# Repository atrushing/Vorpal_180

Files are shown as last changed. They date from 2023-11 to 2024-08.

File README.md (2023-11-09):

# Vorpal 180 -- PRE-RELEASE --

    A printed printer

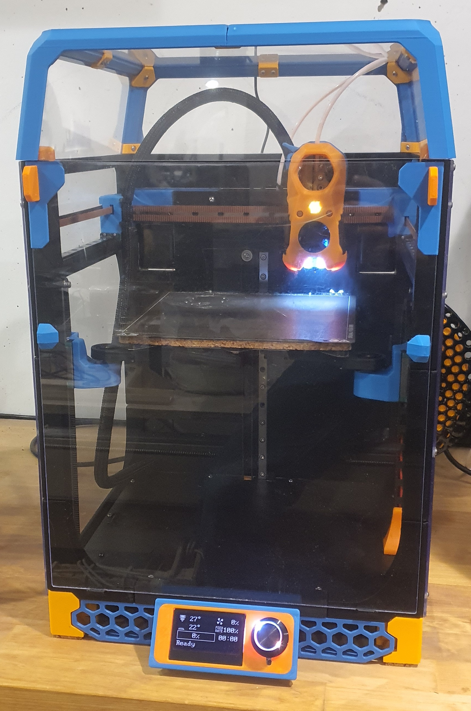
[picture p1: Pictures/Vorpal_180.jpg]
Vorpal 180


## Features:

- Print volume: 180 x 180 x 200mm

- Triple belted Z

- 3:1 geared Z with Nema 17 steppers or 5:1 with Nema 14 pancake steppers

- MGN12  X axis

- MGN9 option for Boop compatibility

- MGN9  Y and Z axes

- Design based on Voron V0.1 and Trident printers

- Bed and sub-plate from Prusa Mini

- Uses printed flexures instead of GE5C bearings for build plate mounting

- Hidden handles in side skirts

- Hinged locking tophat

- Mini Stealth toolhead compatible - [1.5](https://www.teamfdm.com/files/file/606-mini-stealth-orbiter-15/) [2.0](https://www.teamfdm.com/files/file/612-mini-stealth-orbiter-20/) [LGX](https://www.teamfdm.com/files/file/616-mini-stealth-lgx-lite/) [Sherpa](https://www.teamfdm.com/files/file/657-mini-stealth-mini-sherpa/)

- Manta M8P control board

Learn more and follow the development process on [TeamFDM.com](https://www.teamfdm.com/forums/topic/1886-vorpal-180-a-printed-printer/)

[Support me](https://paypal.me/atrushing)

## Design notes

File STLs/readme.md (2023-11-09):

## Filament Required

### Base color
- 900 grams

### Primary color
- 500 grams

### Accent color
- 200 grams

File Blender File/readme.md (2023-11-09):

This project was developed entirely in Blender. The official geometry is found in the STLs folder and only exists in mesh format.

The .blend file provided here is intended as a reference for assembly and modding purposes.

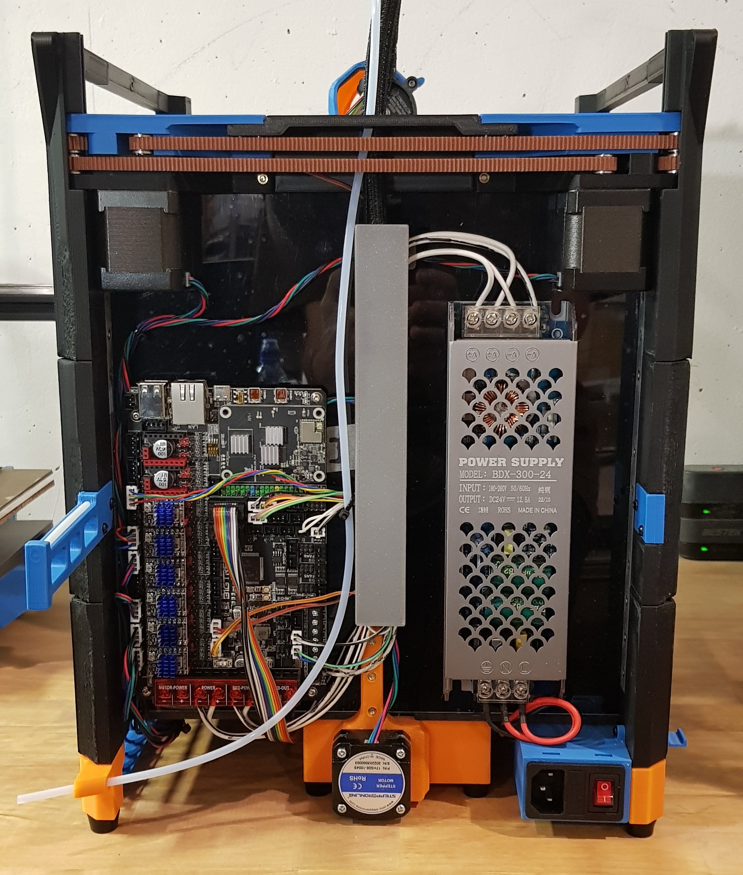
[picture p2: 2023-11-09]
Pictures/Electronics_bay.jpg

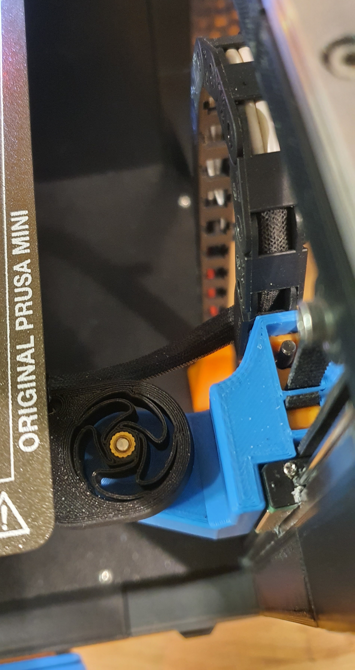
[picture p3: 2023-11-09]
Pictures/Z Bed Joint Flexure.jpg

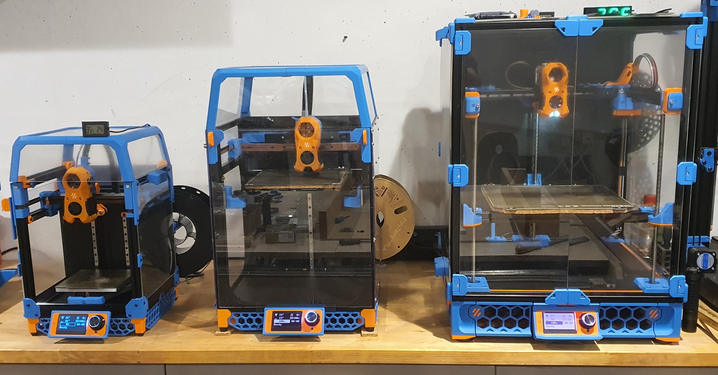
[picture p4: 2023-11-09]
Pictures/Comparison.jpg

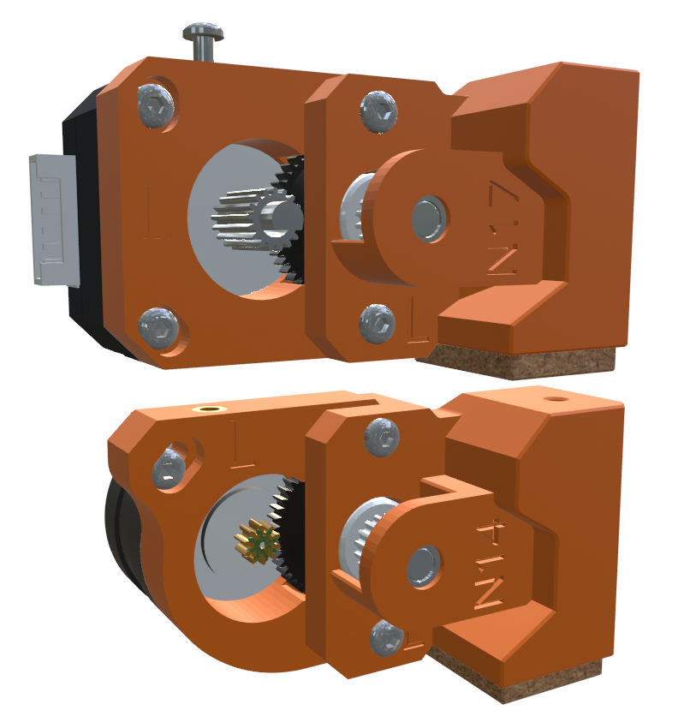
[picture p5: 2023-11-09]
Pictures/Belt driven Z axis options.png

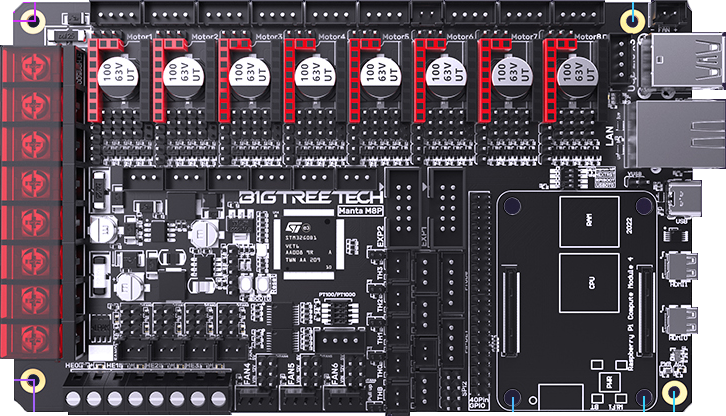
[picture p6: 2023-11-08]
Blender File/BTT_Manta_M8P_cr.png

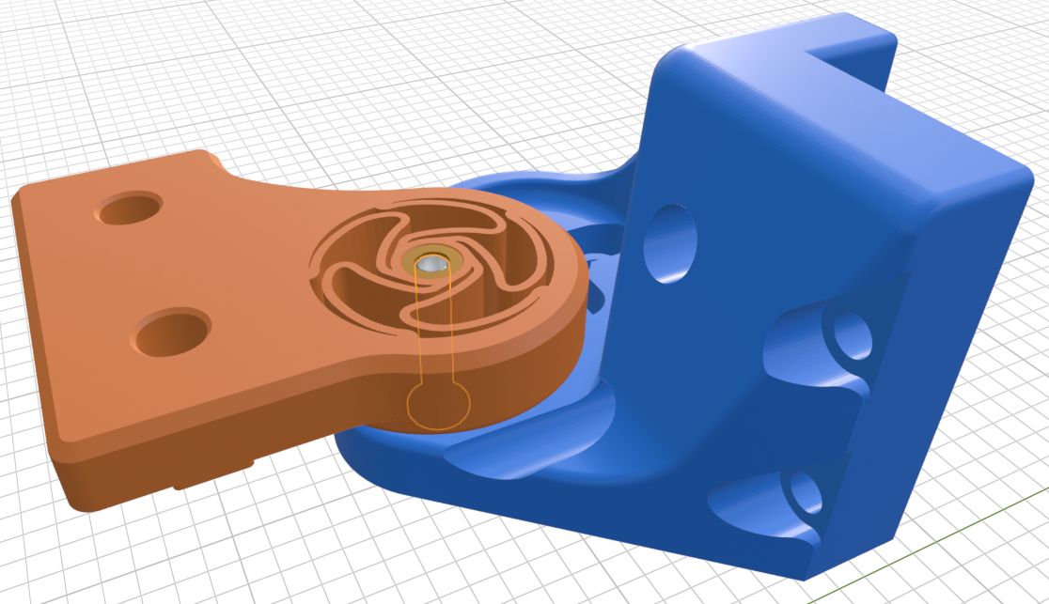
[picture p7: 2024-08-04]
STLs/Z_Axis/Trident_Flexures/Trident_Flexures.png

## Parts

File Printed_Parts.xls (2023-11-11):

Group | Name | Qty | Color | Finished | Source | License
Base | [a]_12864_display_case_front_insert.stl | 1 | Accent
 | [a]_Display_wedge_mount_35deg.stl | 1 | Accent
 | [a]_Foot_rear_left.stl | 1 | Accent
 | [a]_Foot_rear_right.stl | 1 | Accent
 | [p]_12864_display_case_front.stl | 1 | Primary
 | [p]_12864_display_case_rear.stl | 1 | Primary
 | [p]_Door_stow_blank_x2.stl | 2 | Primary
 | [p]_Door_stow_hook_x2.stl | 2 | Primary
 | [p]_Side_skirt_front.stl | 1 | Primary
 | [p]_Side_skirt_left.stl | 1 | Primary
 | [p]_Side_skirt_right.stl | 1 | Primary
Nema 14 | [a]_Foot_front_left_Nema14.stl | option | Accent
 | [a]_Foot_front_right_Nema14.stl | option | Accent
 | [a]_Motor_mount_front_left_Nema14.stl | option | Accent
 | [a]_Motor_mount_front_right_Nema14.stl | option | Accent
 | [a]_Motor_mount_rear_Nema14.stl | option | Accent
 | [a]_Z_axis_drive_rear_Nema14.stl | option | Accent
Nema 17 | [a]_Foot_front_left_Nema17.stl | 1 | Accent
 | [a]_Foot_front_right_Nema17.stl | 1 | Accent
 | [a]_Motor_mount_front_left_Nema17.stl | 1 | Accent
 | [a]_Motor_mount_front_right_Nema17.stl | 1 | Accent
 | [a]_Motor_mount_rear_Nema17.stl | 1 | Accent
 | [a]_Z_axis_drive_rear_Nema17.stl | 1 | Accent
 |  | 19
Electronics Bay | [p]_Manta_M8P_mounts.stl | 1 set | Primary
 | [p]_Power_inlet.stl | 1 | Primary
 | [p]_Spool_holder.stl | 1 | Primary
 | [p]_Spool_holder_blank.stl | 1 | Primary
 | [p]_Wire_guide.stl | 1 | Primary |  | remixed from https://www.printables.com/model/118343-cable-rail-cable-guide | Public Domain | https://creativecommons.org/share-your-work/public-domain/cc0/
 | [p]_Wire_guide_cover.stl | 1 | Primary |  | remixed from https://www.printables.com/model/118343-cable-rail-cable-guide | Public Domain | https://creativecommons.org/share-your-work/public-domain/cc0/
 | [p]_Z_axis_rear_stiffener_x2.stl | 2 | Primary
 |  | 8
Frame | [b]_AB_drive_frame_center.stl | 1 | Base
 | [b]_A_drive_frame_lower.stl | 1 | Base
 | [b]_A_drive_frame_upper.stl | 1 | Base
 | [b]_B_drive_frame_lower.stl | 1 | Base
 | [b]_B_drive_frame_upper.stl | 1 | Base
 | [b]_Frame_center_connector_left.stl | 1 | Base
 | [b]_Frame_center_connector_right.stl | 1 | Base
 | [b]_Frame_front_lower_connector.stl | 1 | Base
 | [b]_Frame_front_lower_left.stl | 1 | Base
 | [b]_Frame_front_lower_right.stl | 1 | Base
 | [b]_Frame_front_upper_left.stl | 1 | Base
 | [b]_Frame_front_upper_right.stl | 1 | Base
 | [b]_Frame_front_vertical_connector_left.stl | 1 | Base
 | [b]_Frame_front_vertical_connector_right.stl | 1 | Base
 | [b]_Frame_lower_connecter_left.stl | 1 | Base
 | [b]_Frame_lower_connecter_right.stl | 1 | Base
 | [b]_Frame_rear_lower_left.stl | 1 | Base
 | [b]_Frame_rear_lower_right.stl | 1 | Base
 | [b]_Frame_rear_upper_left.stl | 1 | Base
 | [b]_Frame_rear_upper_right.stl | 1 | Base
 | [b]_Frame_rear_vertical_connector_left.stl | 1 | Base
 | [b]_Frame_rear_vertical_connector_right.stl | 1 | Base
 | [b]_Frame_upper_connector_left.stl | 1 | Base
 | [b]_Frame_upper_connector_right.stl | 1 | Base
 |  | 24
Gantry | [a]_AB_tension_idler_new_x2.stl | 2 | Accent
 | [a]_AB_tension_idler_old_x2.stl | 2 | Accent
 | [p]_X_Axis_brace_MGN9_left.stl | option | Primary
 | [p]_X_Axis_brace_MGN9_right.stl | option | Primary
 | [p]_X_Axis_brace_MGN12_left.stl | 1 | Primary
 | [p]_X_Axis_brace_MGN12_right.stl | 1 | Primary
 | [p]_x_frame_Mini_Stealth_MicroProbe_left.stl | 1 | Primary
 | [p]_x_frame_Mini_Stealth_MicroProbe_right.stl | 1 | Primary
 | [p]_XY_joint_left_lower.stl | 1 | Primary
 | [p]_XY_joint_left_upper.stl | 1 | Primary
 | [p]_XY_joint_right_lower.stl | 1 | Primary
 | [p]_XY_joint_right_upper.stl | 1 | Primary
 |  | 12
Panels | [a]_door_panel_pinch_handle_x2.stl | 2 | Accent
 | [p]_door_panel_magnet_latch_x4.stl | 4 | Primary
 | [p]_3mm_door_panel_corner_top_left.stl | 1 | Primary
 | [p]_3mm_door_panel_corner_top_right.stl | 1 | Primary
 |  | 8
 | 3mm_back_aux_panel_black.stl | 1 | black
 | 3mm_back_main_panel_black.stl | 1 | black
 | 3mm_door_panel_clear.stl | 1 | clear
 | 3mm_side_left_panel_clear.stl | 1 | clear
 | 3mm_side_right_panel_clear.stl | 1 | clear
 | 3mm_tophat_front-back_panel_clear_x2.stl | 2 | clear
 | 3mm_tophat_side_panel_clear_x2.stl | 2 | clear
 | 3mm_tophat_top_panel_clear.stl | 1 | clear
 | 4mm_bottom_panel_black.stl | 1 | black
 |  | 11
Tools | AB_pulley_jig.stl | 1
 | Calibration_square_100mm.stl | 1
 | Calibration_square_100mm_base.stl | 1
 | Kezat_Hex_Bit_Driver_Short_Thumb_Crown.stl | 3 |  |  | remixed from https://www.printables.com/model/16567-screwdriver | CC4 Attribution | http://creativecommons.org/licenses/by/4.0/
 | Hex Bit Set |  |  |  | https://www.amazon.de/-/en/Racing-4-Piece-Metric-Electric-Screw/dp/B097NF94SL/
 | MicroSD_card_tweezers.stl | 1
 | Snap_pin_x26.stl | 26 | Primary |  | https://www.thingiverse.com/thing:213310 | CC3 Attribution | https://creativecommons.org/licenses/by-sa/3.0/
 |  | 33
Top Hat | [a]_Tophat_clips_plate.stl | 1 set | Accent
 | [p]_tophat_latch_thumbscrew_x2.stl | 2 | Primary
 | [p]_Tophat_part_front_left.stl | 1 | Primary
 | [p]_Tophat_part_front_right.stl | 1 | Primary
 | [p]_Tophat_part_rear_left.stl | 1 | Primary |  | remixed from https://www.teamfdm.com/files/file/327-tophathingev01/ | GPL v3
 | [p]_Tophat_part_rear_right.stl | 1 | Primary |  | remixed from https://www.teamfdm.com/files/file/327-tophathingev01/ | GPL v3
 | [p]_Unibody_Tophat.stl | option | Primary
 |  | 7
Z Axis | [a]_belt_lock_wedge_x3.stl | 3 | Accent
 | [a]_belt_tension_slider_left.stl | 1 | Accent
 | [a]_belt_tension_slider_rear.stl | 1 | Accent
 | [a]_belt_tension_slider_right.stl | 1 | Accent
 | [a]_Cable_chain_mount_base.stl | 1 | Accent
 | [b]_Cable_chain_guide.stl | 1 | Base
 | [b]_Z_bed_left.stl | 1 | Base
 | [b]_Z_bed_rear.stl | 1 | Base
 | [b]_Z_bed_right.stl | 1 | Base
 | [p]_Z_carriage_left.stl | 1 | Primary
 | [p]_Z_carriage_rear.stl | 1 | Primary
 | [p]_Z_carriage_right.stl | 1 | Primary
 |  | 14

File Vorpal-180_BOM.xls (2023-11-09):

Movement |  |  |  |  |  |  | €
MGN9H | 5 | 250mm | €12.48 | €62.40 | Amazon.com
MGN12H | 1 | 250mm | €17.01 | €17.01 | Amazon.com
GT2 belt | 1 | 4m20 | €15.59 | €14.99 | Amazon.com
GT2 16T Pulley | 3 | 5mm bore | €1.40 | €4.20 | Amazon.com
Nema17 x 20 | 3 | Z Axis | €7.46 | €22.38 | https://www.omc-stepperonline.com/nema-17-bipolar-1-8deg-16ncm-22-6oz-in-1a-3-7v-42x42x20mm-4-wires-17hs08-1004s
Option |  | LDO | €22.46 |  | https://www.aliexpress.com/item/1005002899860754.html
Nema17 x 40 | 2 | A/B Motors | €9.94 | €19.88 | https://www.omc-stepperonline.com/nema-17-bipolar-45ncm-64oz-in-2a-42x42x40mm-4-wires-w-1m-cable-connector-17hs16-2004s1
BMG Kit | 3 | Z axis reduction | €5.07 | €15.21 | https://www.aliexpress.com/item/1005004946578945.html
F623 Flanged Bearing | 30 | Belt management | €1.44 | €43.20 | Amazon.com
M3x6x0.5 Shim | 45 | 3 shims per 2 bearings | €0.12 | €5.31 | Amazon.com
3mm x 20mm steel shaft | 4 | pin mod for XY-joints
Toolhead
4010 Blower | 2 | 24V | €4.48 | €8.96 | Amazon.com
3007/3010 fan | 1 | 5V/24V | €3.90 | €3.90 | Amazon.com
BMG Kit | 1 | Mini/Micro Sherpa | €5.07 | €5.07 | https://www.aliexpress.com/item/1005004946578945.html
Nema14 Pancake 20mm long | 1 | StepperOnline | €9.15 | €9.15 | https://www.omc-stepperonline.com/nema-14-high-temp-stepper-motor-10ncm-14-24oz-in-insulation-class-h-180c-14re08-1004s-h
4mm OD x 2mm ID PTFE tube |  | ~50mm
Phaetus Dragonfly | 1 |  | €61.32 | €61.32 | 3Djake.com
24V 50W heater + Thermistor | 1 |  | €4.99 | €4.99 | Amazon.com
Extra
7x7mm Cable Chain | 1 | 40cm | €9.73 | €9.73 | Amazon.com
M3 HeatSet Inserts | 100 | M3x4x5 | €0.08 | €8.30 | Amazon.com | 120 pcs for $10.03
Rubber Feet 15x12x8mm | 6 |  | 0.58 | 3.48 | Amazon.com
6mm cork 20x25mm feet | 4 |  | €0.15 | €0.60 | local
4mm OD x 3mm ID PTFE tube | 1 | reverse bowden | €5.94 | €5.94 | Amazon.com
3x6mm magnets | 8 | door latching
Buildplate
Prusa Mini bed + PEI Buildplate | 1 |  | €44.66 | €44.66 | https://www.aliexpress.com/item/4000898386404.html
Official Prusa spring steel sheet | 1 | worth getting the original | €30.00 |  | https://www.prusa3d.com/product/mini-double-sided-textured-pei-powder-coated-spring-steel-sheet/
Prusa Mini subplate | 1 |  | €15.97 | €15.97 | https://www.aliexpress.com/item/4000761390845.html
6mm x 3mm standoff 6mm long | 9 |  | €0.20 | €1.77 | https://www.aliexpress.com/item/33002300459.html
M3x16 FHCS | 9 |  | €0.15 | €1.35 | Amazon.com
GE5C Joint bearing | 3 |  | €2.14 | €6.42 | https://www.aliexpress.com/item/1005001865254355.html
6mm thick cork | 1 |  | €1.56 | €1.56 | local
Electronics
24V 300W Power Supply | 1 |  | €21.47 | €21.47 | https://www.aliexpress.com/item/32826453801.html
BTT Manta M8P w/ CB1 +TMC2209 | 1 |  | €98.68 | €98.68 | https://biqu.equipment/collections/control-board/products/manta-m4p-m8p?variant=39847239155810
BTT Mini 12864 | 1 |  | €12.68 | €12.68
Biqu MicroProbe | 1 |  | €27.28 | €27.28 | https://biqu.equipment/products/microprobe-v1-0-for-b1-printers-h2-extruders-ender-3
Power Inlet | 1 |  | €11.29 | €11.29 | Amazon.com
 |  |  |  | €559.25

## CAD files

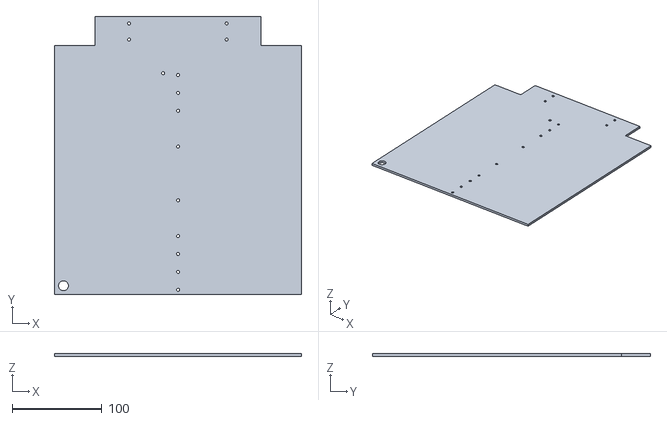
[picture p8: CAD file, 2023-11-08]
STLs/Panels/3mm_back_main_panel_black.stl
276.0 x 311.1 x 3.00

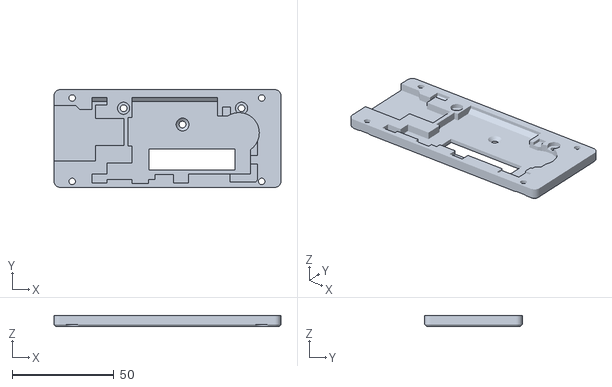
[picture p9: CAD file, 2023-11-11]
STLs/Base/[p]_12864_display_case_rear.stl
111.6 x 48.1 x 5.51

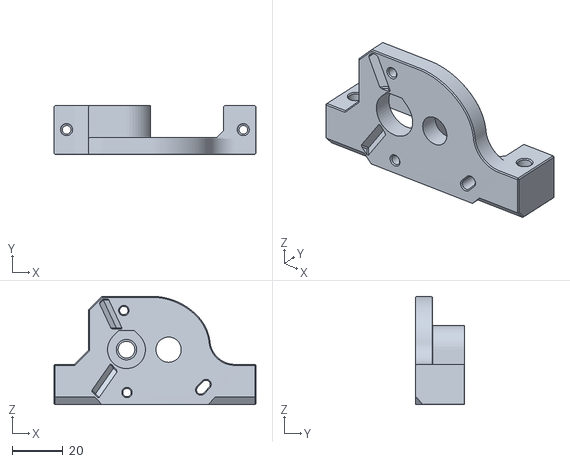
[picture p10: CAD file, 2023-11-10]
STLs/Base/Nema_14_option/[a]_Z_axis_drive_rear_Nema14.stl
80.0 x 19.4 x 42.9

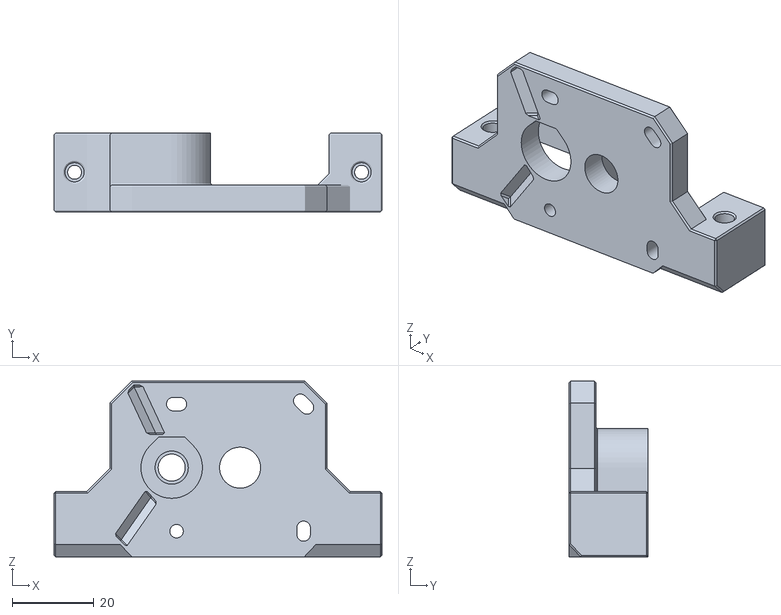
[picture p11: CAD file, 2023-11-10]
STLs/Base/Nema_17_option/[a]_Z_axis_drive_rear_Nema17.stl
80.0 x 19.3 x 42.9

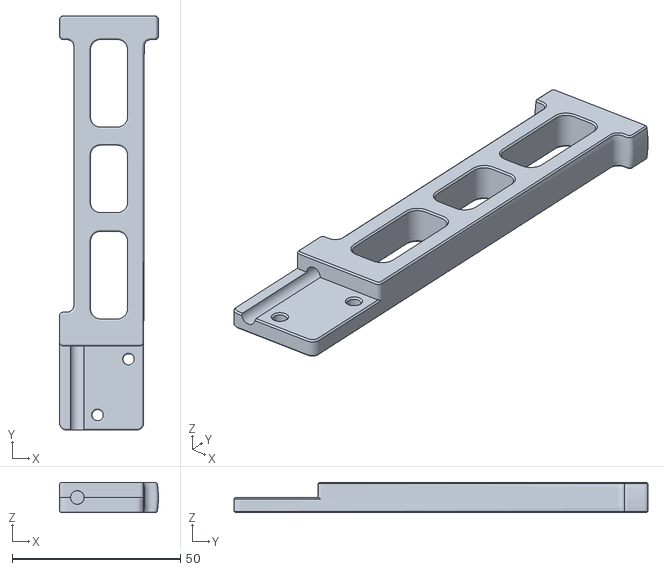
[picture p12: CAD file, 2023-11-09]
STLs/Electronics_bay/[p]_Spool_holder.stl
29.4 x 123.0 x 9.00

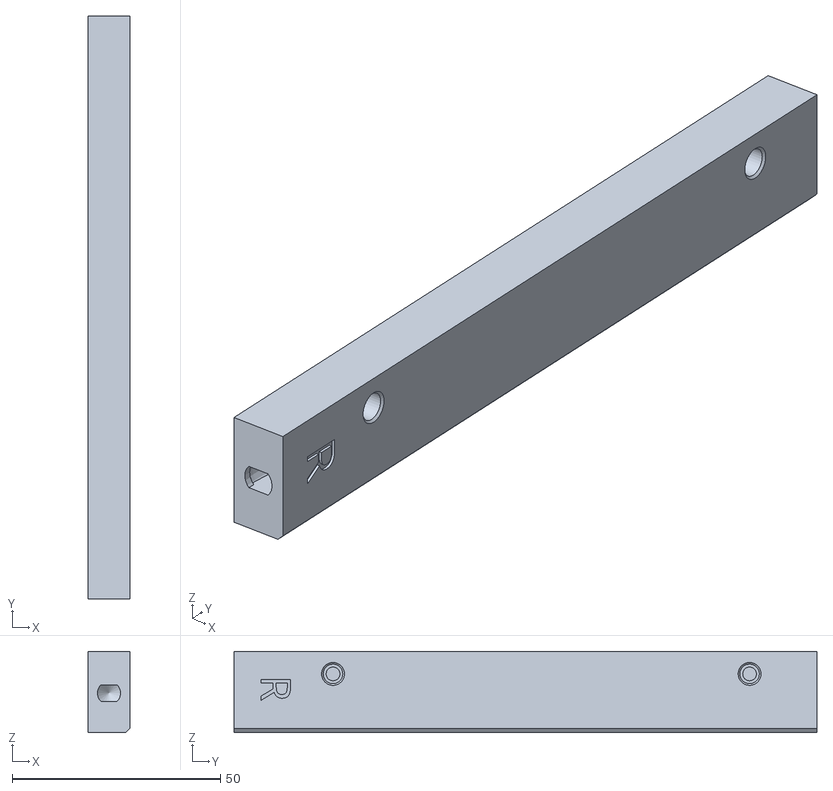
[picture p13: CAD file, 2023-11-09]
STLs/Frame/[b]_Frame_center_connector_right.stl
10.0 x 140.0 x 19.5

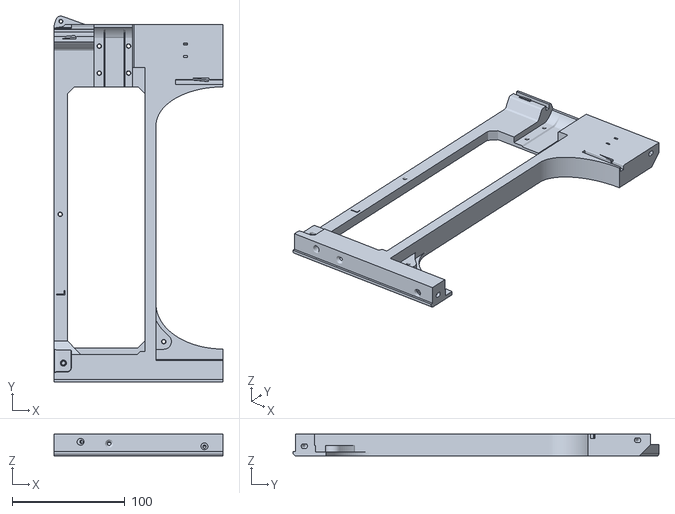
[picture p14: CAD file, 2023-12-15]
STLs/Frame/Big Printers/[b]_Frame_Left_upper.stl
150.0 x 324.9 x 19.5

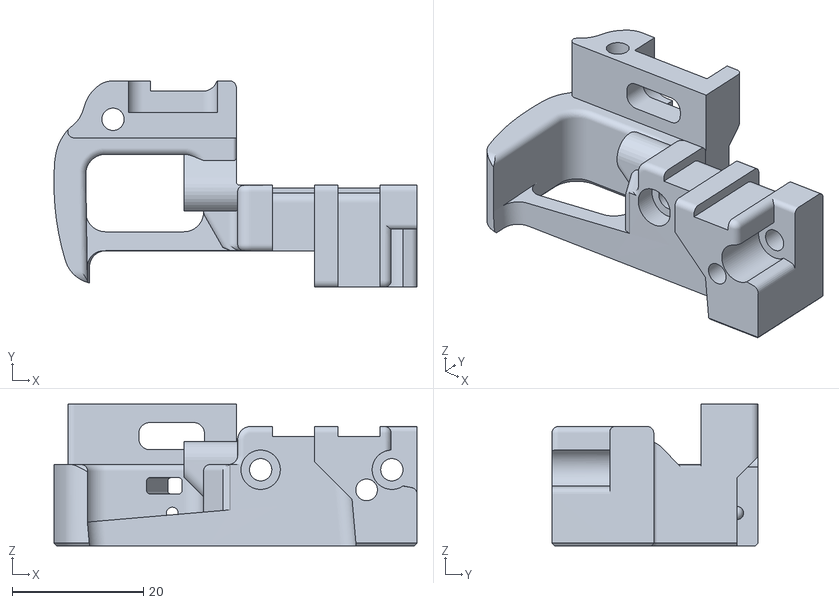
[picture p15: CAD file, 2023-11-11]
STLs/Gantry/[p]_x_frame_Mini_Stealth_MicroProbe_right.stl
55.3 x 31.4 x 21.6

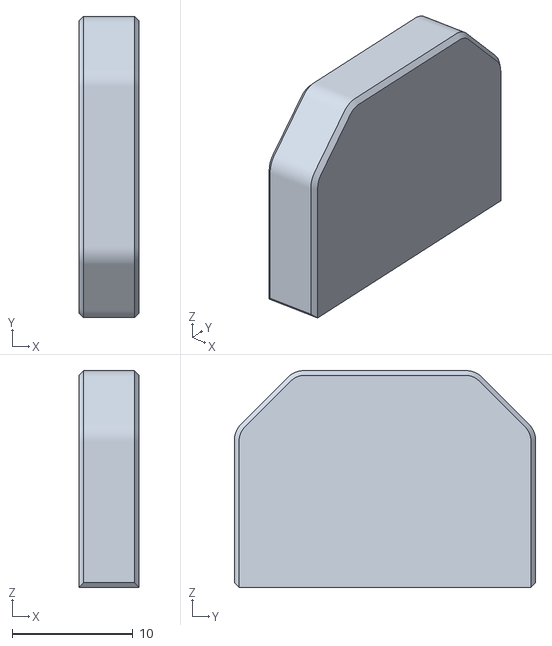
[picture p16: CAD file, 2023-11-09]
STLs/Panels/[a]_door_panel_pinch_handle_x2.stl
5.00 x 25.0 x 18.0

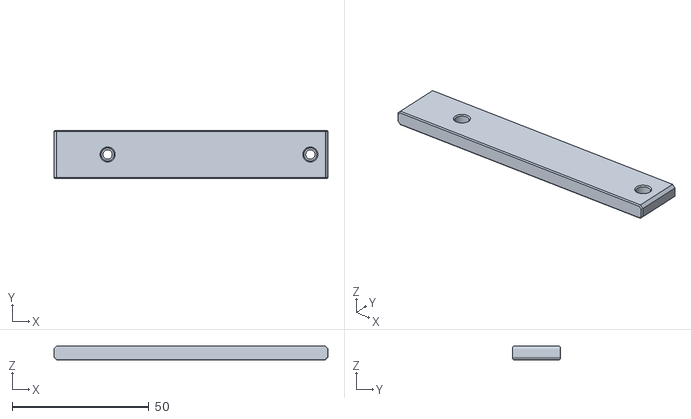
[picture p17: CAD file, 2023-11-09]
STLs/Tools/Calibration_square_100mm_base.stl
100.0 x 17.6 x 5.00

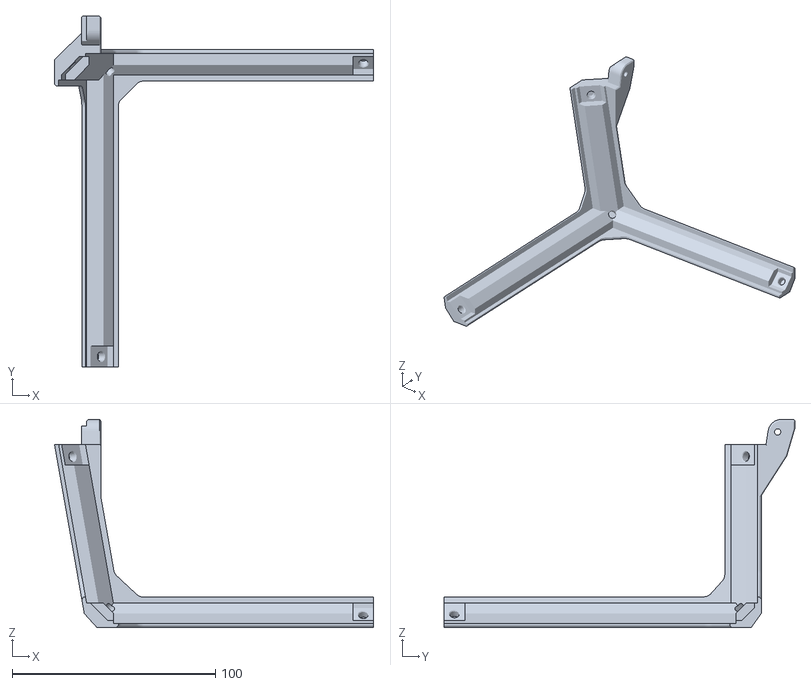
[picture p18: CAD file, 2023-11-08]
STLs/TopHat/[p]_Tophat_part_rear_right.stl
156.9 x 172.4 x 102.4

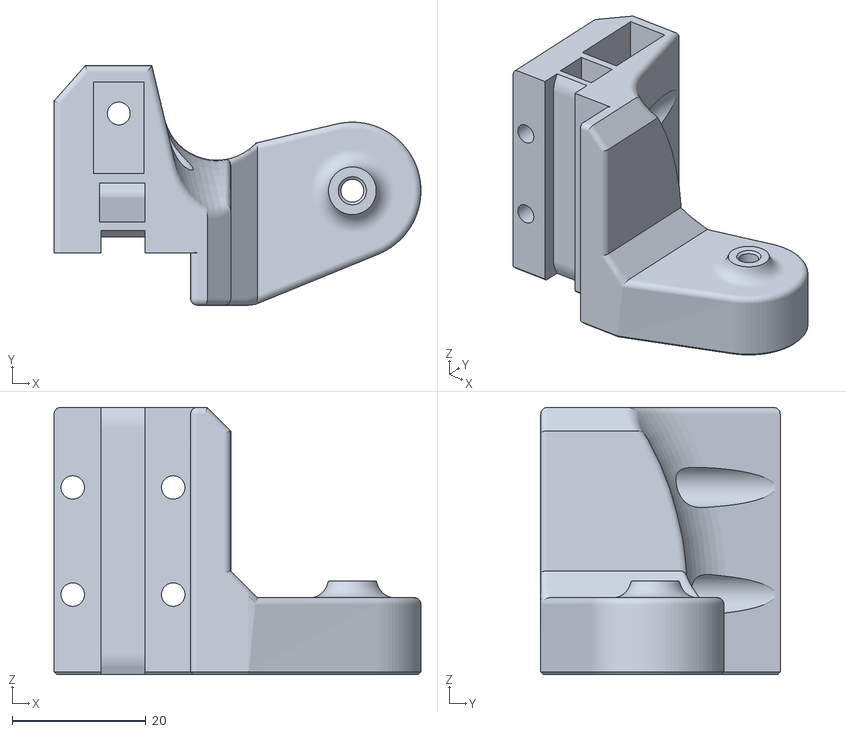
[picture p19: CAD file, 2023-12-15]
STLs/Z_Axis/[p]_Z_carriage_left_UHF.stl
54.8 x 35.8 x 39.9

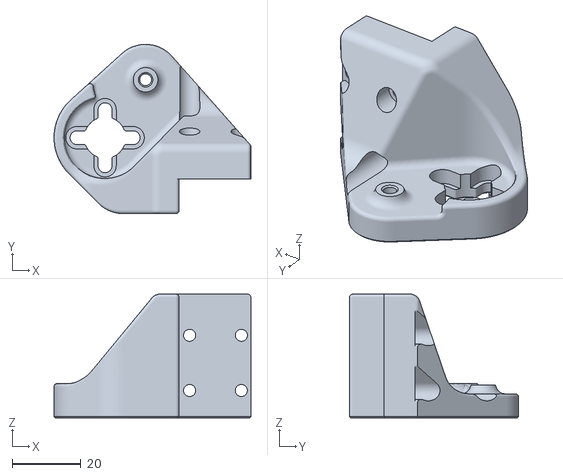
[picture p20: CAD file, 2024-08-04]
STLs/Z_Axis/Trident_Flexures/z_carriage_right_M3_Flexure.stl
57.1 x 49.1 x 35.9

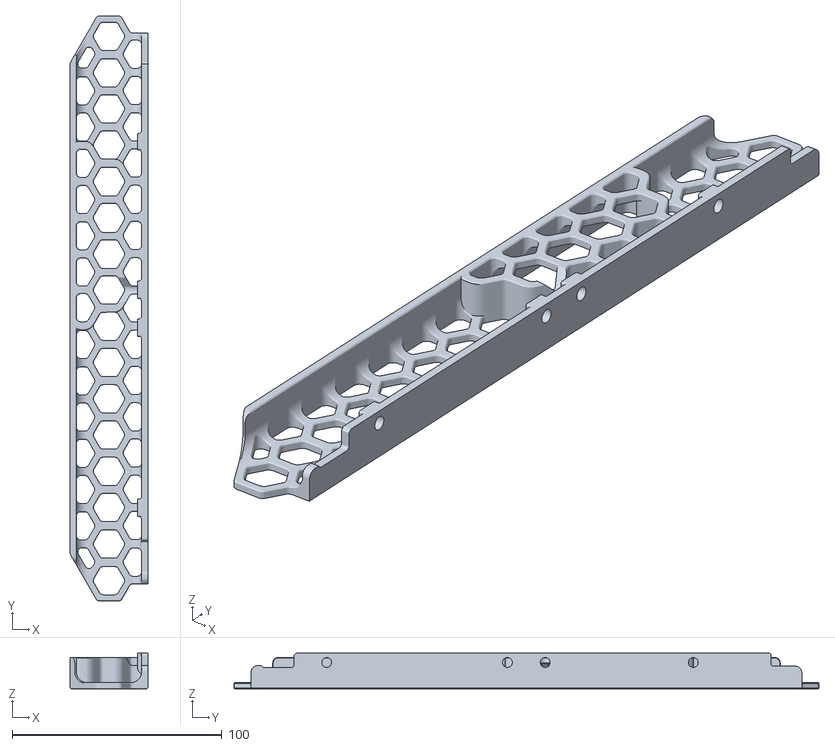
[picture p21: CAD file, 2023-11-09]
STLs/Base/[p]_Side_skirt_right.stl
37.0 x 278.7 x 17.0

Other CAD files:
STLs/Base/Nema_14_option/[a]_Motor_mount_rear_Nema14.stl
STLs/Base/Nema_17_option/[a]_Motor_mount_rear_Nema17.stl
STLs/Electronics_bay/[p]_Wire_guide_cover.stl
STLs/Frame/[b]_Frame_rear_vertical_connector_right.stl
STLs/Base/Nema_14_option/[a]_Foot_front_left_Nema14.stl
STLs/Base/Nema_14_option/[a]_Foot_front_right_Nema14.stl
STLs/Base/Nema_14_option/[a]_Motor_mount_front_left_Nema14.stl
STLs/Base/Nema_14_option/[a]_Motor_mount_front_right_Nema14.stl
STLs/Base/Nema_17_option/[a]_Foot_front_left_Nema17.stl
STLs/Base/Nema_17_option/[a]_Foot_front_right_Nema17.stl
STLs/Base/Nema_17_option/[a]_Motor_mount_front_left_Nema17.stl
STLs/Base/Nema_17_option/[a]_Motor_mount_front_right_Nema17.stl
STLs/Base/[a]_12864_display_case_front_insert.stl
STLs/Base/[a]_Display_wedge_mount_35deg.stl
STLs/Base/[a]_Foot_rear_left.stl
STLs/Base/[a]_Foot_rear_right.stl
STLs/Base/[p]_12864_display_case_front.stl
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

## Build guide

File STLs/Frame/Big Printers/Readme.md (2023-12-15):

A 400mm printer is needed to print the side frames in one solid piece. There are also two-piece side frames that can fit on a 350mm printer.
There has been no shrinkage compensation applied to these pieces as different printers and filaments will have different shrink factors. Check the Tools folder for the calibration_square and follow the process in the manual to calculate a good print scale.

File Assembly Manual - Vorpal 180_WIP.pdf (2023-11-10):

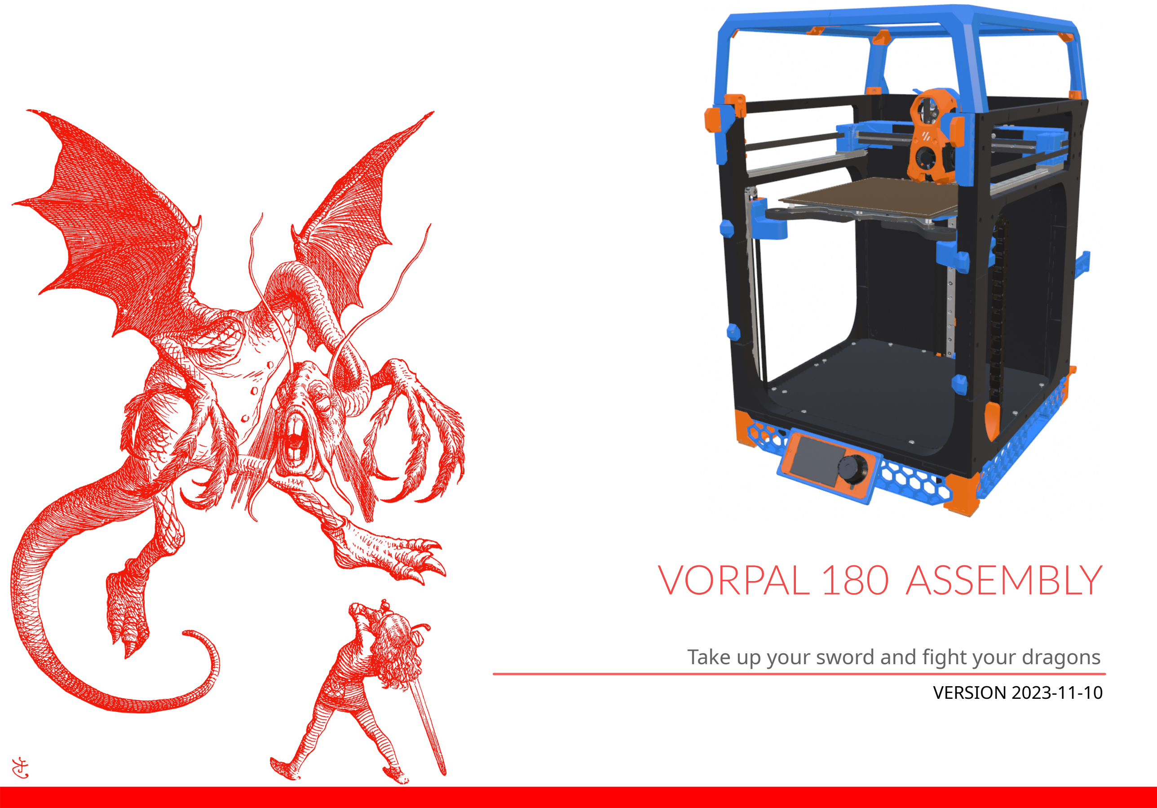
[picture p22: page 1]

# VORPAL 180 ASSEMBLY

## Take up your sword and fight your dragons

## VERSION 2023-11-10

## Preparation

## TABLE OF CONTENTS

03

Hardware | 05
Tools | 06
Z Drives Assembly (Nema 14) | 08
Z Drives Assembly (Nema 17) | 04
Preparation | 04
Preparation | 04
Preparation | 04
Preparation | 04
Preparation | 04
Preparation | 04
Preparation | 04
Preparation | 04
Preparation | 04
Preparation | 04

2

## PREPARATION

PART PRINTING GUIDELINES

3D PRINTING PROCESS

MATERIAL

LAYER HEIGHT

EXTRUSION WIDTH

INFILL TYPE

INFILL PERCENTAGE

WALL COUNT

SOLID TOP/BOTTOM LAYERS

COLORS AND QUANTITIES

This printer was designed to utilize the Voron process as much as possible. Their material and print settings should be followed to ensure a mechanically sound machine.

All .stl files with a suffix of "xN" need to be printed N times. Any .stl file without an "x2" style suffix is a unique part in the assembly of the printer.

The color naming convention is as follows:

[b]_xxxx.stl → Base Color
[p]_xxxx.slt → Primary Color [a]_xxxx.stl → Accent Color

Fused Deposition Modeling (FDM)

ABS

Recommended: 0.2mm

Recommended: Forced 0.4mm

Grid, Gyroid, Honeycomb, Triangle or Cubic

Recommended: 40%

INFILL TYPE: FRAME PIECES
Cubic

Recommended: 4

Recommended: 5

3

PRINT CALIBRATION
The Calibration_square_100mm.stl is provided in the Tools folder to help verify the dimensional accuracy and squareness of the printer/material used to produce parts for the Vorpal 180. ABS has a rather high shrinkage ratio and this needs to be accounted for while printing. With the larger printed pieces of the Vorpal design, accuracy becomes more crucial.

By measuring the Calibration Square with calipers, you can determine the X and Y shrinkage factor for your printer/ material. Measure the X and Y dimensions separately and use the equation below to find a value to put into your slicing software.

10000 / [measured] = ScalingFactor
example:
X → 10000 / 99.32mm = 100.68
Y → 10000 / 99.48mm = 100.52

You can use each of these values separately or take the average and use that for both X and Y. The Z axis shrinkage is not usually an issue and should be left at 100.0. In your slicer I suggest manually setting the X/Y scale factors for every printed part. This cannot be applied to the released files because each printer and material will have unique values. This process is different and more accurate than the XY Size Compensation setting found in some slicers but will not address issues such as holes being undersized or part thickness accuracy due to over/under extrusion. A whole build plate can be scaled at once. Just be sure to uncheck the lock icon.

Using different brands of ABS or using a mix of ABS and ASA parts might require separate calibrations per material/printer.

Another feature of the Calibration Square is the inclusion of 3mm holes with 20mm spacing. When calibrated well, each row of holes should line up with the holes of an MGN9 rail and allow a full row of M3 screws to be installed with no binding. The Z_axis_rear_stiffener_x2.stl in the Electronics Bay folder is a good part for verifying the scale factor due to its length and its hole pattern that should also align with an MGN9 linear rail.

The Calibration Square can also be used to verify the squareness of the printer being used to generate parts. Using a pair of heat-set inserts and M3x20 BHCS, it can be assembled with its Base in order to follow the method described in the video linked below. Keep in mind that the measured error is double the actual mm out-of-square per 100mm of the printers' gantry.

If the lines diverge from the bottom to the top then the right side of the gantry needs to be brought forward. If the lines converge from the bottom to the top then the left side needs to be adjusted towards the front of the printer.

## PREPARATION

4

https://youtu.be/hvVK2lOirBM?t=185

## HARDWARE

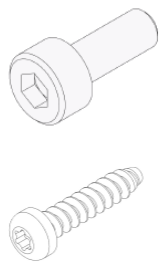
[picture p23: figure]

BUTTON HEAD CAP SCREW (BHCS)

FLAT HEAD CAP SCREW (FHCS)

ISO 7380-1

ISO 10642

ISO 4762 / DIN 912

ISO 10511/DIN 982

Metric fastener with a domed shaped head and hex drive. Most commonly used fastener in this build.

Metric fastener with a cylindrical head and hex drive. Mostly used for connecting to linear rail carriages.

Metric fastener with a cone shaped head and a flat top.

Fastener with a pronounced thread profile that is screwed directly into plastic.

Hex nut with a nylon filled center which prevents the components from loosening.

SOCKET HEAD CAP SCREW (SHCS)

SELF TAPPING SCREW

LOCK NUT

5

3x6x0.5 DIN 988

DIN 562

Not to be confused with stamped washers. These are used in all M3 call-out locations in this manual.

A ball bearing with a flange used for the gantry and Z axis idler pulleys.

Heat the inserts with a soldering iron so that they melt the plastic when installed. As the plastic cools, it solidifies around the knurls and ridges on the insert for excellent resistance to both torque and pull-out.

16 tooth GT2 drive pulley used on the motion system of the Vorpal 180.

SHIM

Used for the Z belt tensioners.

M3 SQUARE NUT

HEAT SET INSERT

F623 BEARING | PULLEY

## TOOLS

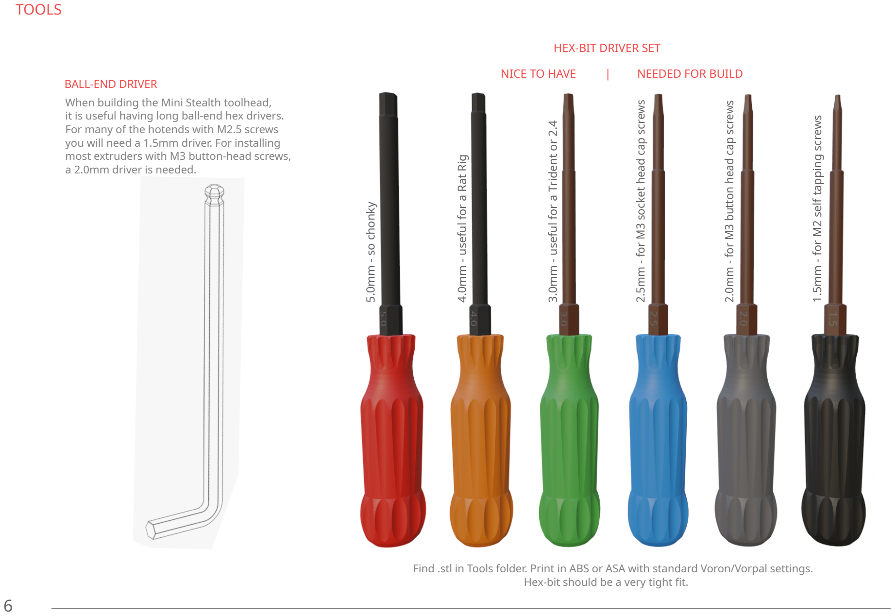
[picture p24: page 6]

6

BALL-END DRIVER

HEX-BIT DRIVER SET
|NICE TO HAVE | NEEDED FOR BUILD

When building the Mini Stealth toolhead, it is useful having long ball-end hex drivers. For many of the hotends with M2.5 screws you will need a 1.5mm driver. For installing most extruders with M3 button-head screws, a 2.0mm driver is needed.

Find .stl in Tools folder. Print in ABS or ASA with standard Voron/Vorpal settings. Hex-bit should be a very tight fit.

5.0mm - so chonky

4.0mm - useful for a Rat Rig

3.0mm - useful for a Trident or 2.4

2.5mm - for M3 socket head cap screws 2.0mm - for M3 button head cap screws 1.5mm - for M2 self tapping screws

This page intentionally left blank

7

## Z DRIVES ASSEMBLY

NEMA 14 OPTION

8

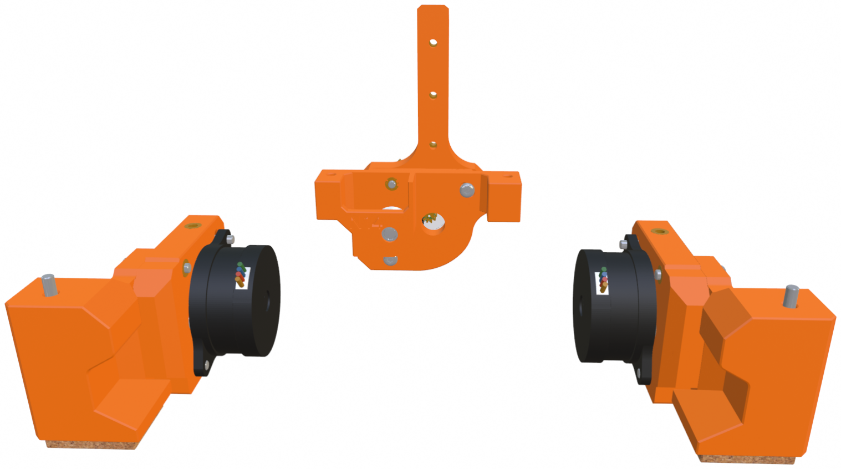
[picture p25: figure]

## COMPONENT PREP

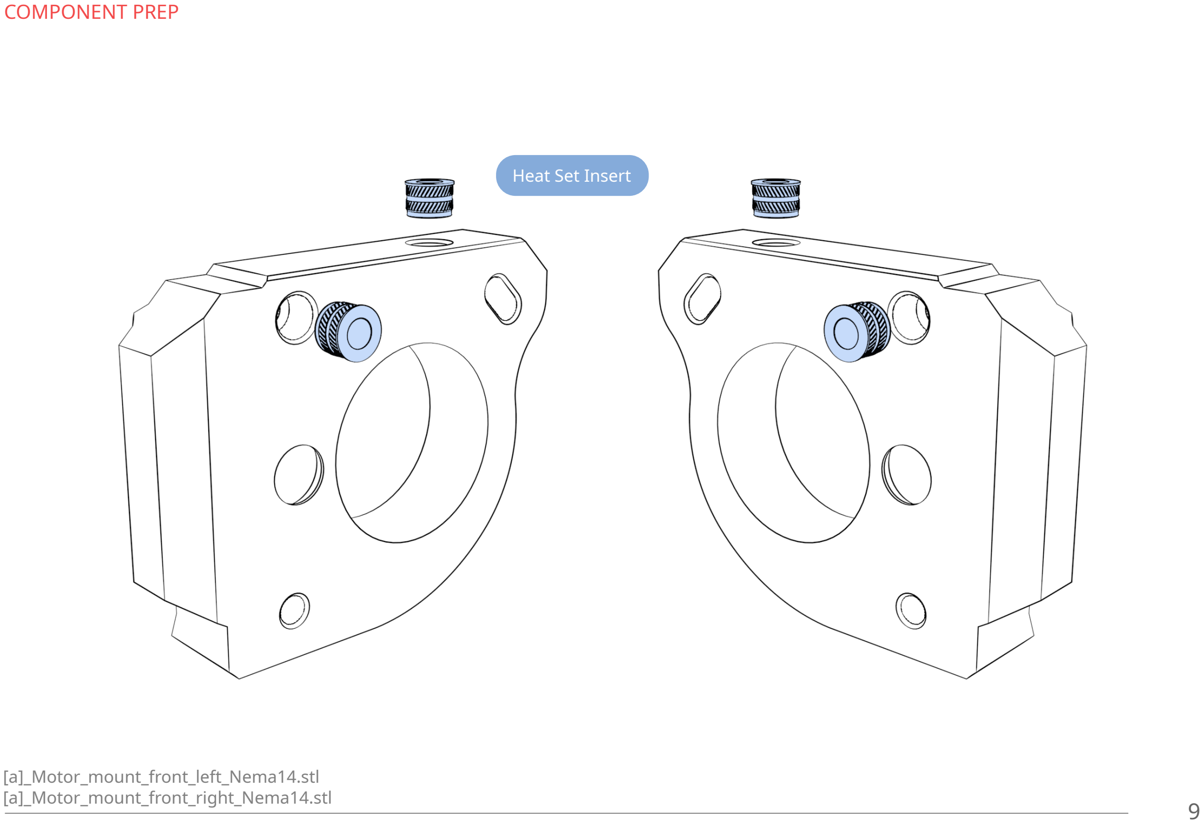
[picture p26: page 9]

[a]_Motor_mount_front_left_Nema14.stl
[a]_Motor_mount_front_right_Nema14.stl | 9

Heat Set Insert

## COMPONENT PREP

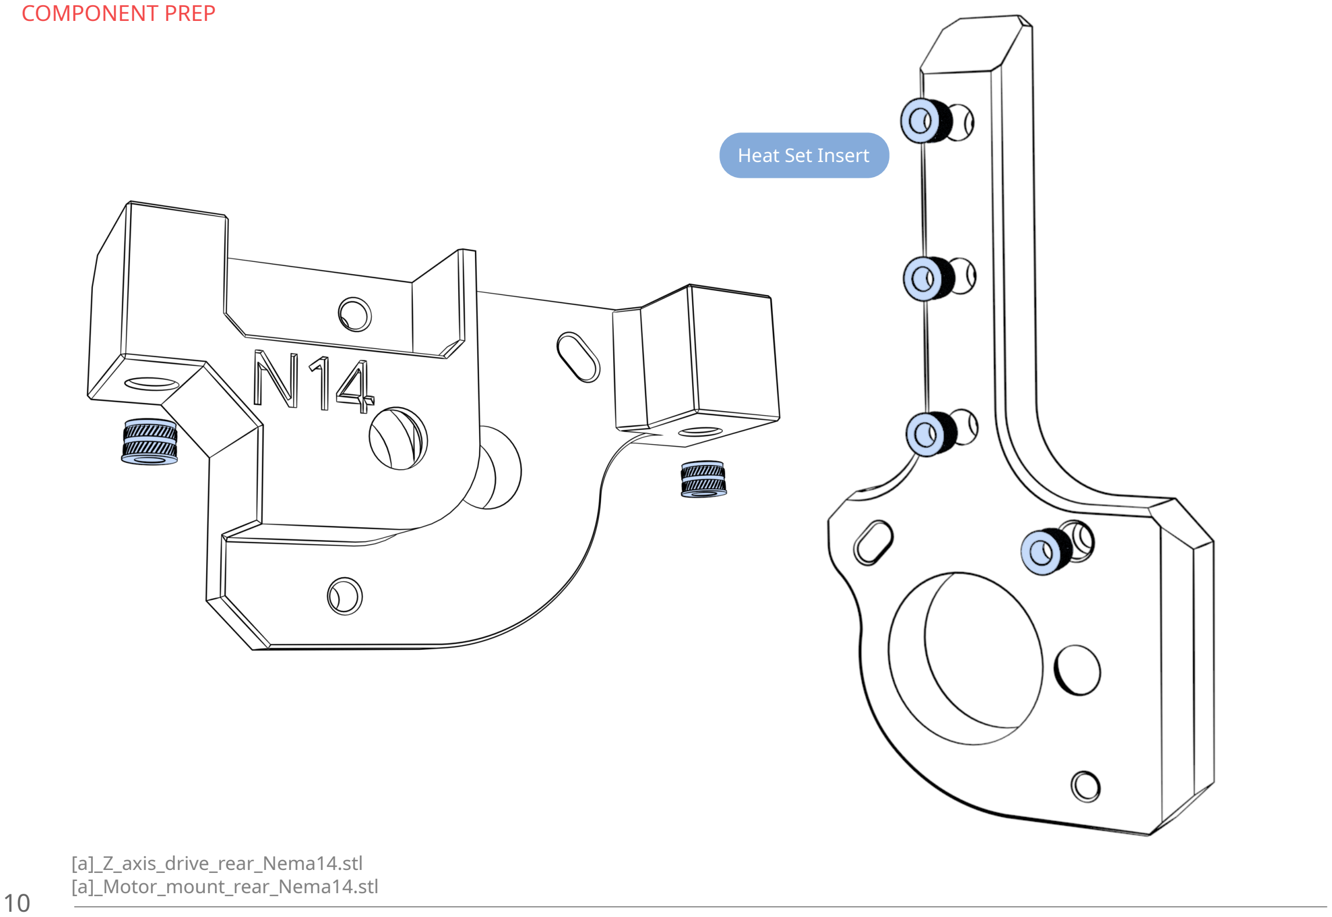
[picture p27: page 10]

[a]_Z_axis_drive_rear_Nema14.stl [a]_Motor_mount_rear_Nema14.stl 10

Heat Set Insert

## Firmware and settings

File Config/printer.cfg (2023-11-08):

# This file contains common pin mappings for the BigTreeTech Octopus V1.
# To use this config, the firmware should be compiled for the STM32F446 with a "32KiB bootloader"
# Enable "extra low-level configuration options" and select the "12MHz crystal" as clock reference

# after running "make", copy the generated "klipper/out/klipper.bin" file to a
# file named "firmware.bin" on an SD card and then restart the OctoPus with that SD card.

# See docs/Config_Reference.md for a description of parameters.

## Voron Design Trident 250/300/350mm BigTreeTech OctoPus V1 TMC2209 UART config

## *** THINGS TO CHANGE/CHECK: ***
## MCU paths                            [mcu] section
## Thermistor types                     [extruder] and [heater_bed] sections
## Leadscrew Rotation Distance          [stepper_z], [stepper_z1], [stepper_z2]
## Z Endstop Switch location            [safe_z_home] section
## Z Endstop Switch  offset for Z0      [stepper_z] section
## PID tune                             [extruder] and [heater_bed] sections
## Probe pin                            [probe] section
## Fine tune E steps                    [extruder] section

# Mainsail settings
[include mainsail.cfg]
[include stealthburner_leds.cfg]
[include macros.cfg]
[include displays.cfg]
[include MicroProbe.cfg]
#[include PIS.cfg]
#[include adxl.cfg]
#[include 9250.cfg]

[mcu]
##  Obtain definition by "ls -l /dev/serial/by-id/" then unplug to verify
##  Obtain UART address by "dmesg | grep tty"
##--------------------------------------------------------------------
serial: /dev/serial/by-id/usb-Klipper_stm32g0b1xx_2A003B000F504B4633373520-if00
# serial: /dev/ttyAMA0
# serial: /dev/serial0
restart_method: command
##--------------------------------------------------------------------

[printer]
kinematics: corexy
max_velocity: 350
max_accel: 5000
max_z_velocity: 70
max_z_accel: 2000
square_corner_velocity: 4.0

[force_move]
#   Set to true to enable FORCE_MOVE and SET_KINEMATIC_POSITION
#   extended G-Code commands. The default is false.
enable_force_move: true

#####################################################################
#   X/Y Stepper Settings
#####################################################################

##  A Stepper - Right
[stepper_x]
step_pin: PE2
dir_pin: !PB4
enable_pin: !PC11
rotation_distance: 32
microsteps: 16
full_steps_per_rotation:200  #set to 400 for 0.9 degree stepper
endstop_pin: PF3
position_min: -5
position_endstop: 191.7
position_max: 192
homing_speed: 80   #Max 100
homing_retract_dist: 5
homing_positive_dir: true

##  Make sure to update below for your relevant driver (2208 or 2209)
[tmc2209 stepper_x]
uart_pin: PC10
interpolate: False
run_current: 0.9
# hold_current: 0.4
sense_resistor: 0.110
stealthchop_threshold: 0 # Set to 999999 to turn stealthchop on, and 0 to use spreadcycle


##  B Stepper - Left
[stepper_y]
step_pin: PF12
dir_pin: !PF11
enable_pin: !PB3
rotation_distance: 32
microsteps: 16
full_steps_per_rotation:200  #set to 400 for 0.9 degree stepper
endstop_pin: PF4
position_min: -4
position_endstop: 180
position_max: 181
homing_speed: 80  #Max 100
homing_retract_dist: 5
homing_positive_dir: true

##  Make sure to update below for your relevant driver (2208 or 2209)
[tmc2209 stepper_y]
uart_pin: PF13
interpolate: False
run_current: 0.9
# hold_current: 0.4
sense_resistor: 0.110
stealthchop_threshold: 0 # 999999


#[input_shaper]
#shaper_freq_x: 50.5  # frequency for the X mark of the test model
#shaper_freq_y: 68.6  # frequency for the Y mark of the test model

#####################################################################
#   Z Stepper Settings
#####################################################################

##  Z0 Stepper - Front Left
[stepper_z]
step_pin: PD7
dir_pin: !PD6
enable_pin: !PF10
rotation_distance: 32
gear_ratio: 50:17
microsteps: 16
endstop_pin: probe:z_virtual_endstop
# position_endstop = 0
##  Z-position of nozzle (in mm) to z-endstop trigger point relative to print surface (Z0)
##  (+) value = endstop above Z0, (-) value = endstop below
##  Increasing position_endstop brings nozzle closer to the bed
##  After you run Z_ENDSTOP_CALIBRATE, position_endstop will be stored at the very end of your config
position_max: 195
position_min: -1.5
homing_speed: 50.0 
second_homing_speed: 10
homing_retract_dist: 3

##  Make sure to update below for your relevant driver (2208 or 2209)
[tmc2209 stepper_z]
uart_pin: PF9
interpolate: False
run_current: 0.5
# hold_current: 0.5
sense_resistor: 0.110
stealthchop_threshold: 0

##  Z1 Stepper - Rear Center
[stepper_z1]
step_pin: PD3
dir_pin: !PD2
enable_pin: !PD5
rotation_distance: 32
gear_ratio: 50:17
microsteps: 16

##  Make sure to update below for your relevant driver (2208 or 2209)
[tmc2209 stepper_z1]
uart_pin: PD4
interpolate: False
run_current: 0.5
# hold_current: 0.5
sense_resistor: 0.110
stealthchop_threshold: 0

##  Z2 Stepper - Front Right
##  Connected to MOTOR_4
[stepper_z2]
step_pin: PC9
dir_pin: PC8
enable_pin: !PD1
rotation_distance: 32
gear_ratio: 50:17
microsteps: 16

##  Make sure to update below for your relevant driver (2208 or 2209)
[tmc2209 stepper_z2]
uart_pin: PD0
interpolate: False
run_current: 0.5
# hold_current: 0.5
sense_resistor: 0.110
stealthchop_threshold: 0


#####################################################################
#   Extruder
#####################################################################

#   Connected to MOTOR_6
#   Heater - HE0
#   Thermistor - T0
[extruder]
step_pin: PA10
dir_pin: PA14
enable_pin: !PA15
##  Update value below when you perform extruder calibration
##  If you ask for 100mm of filament, but in reality it is 98mm:
##  rotation_distance = <previous_rotation_distance> * <actual_extrude_distance> / 100
##  22.6789511 is a good starting point
rotation_distance: 4.637  # orbiter motor LDO-36STH20-1004AHG(XH)
##  Update Gear Ratio depending on your Extruder Type
##  Use 50:17 for Afterburner/Clockwork (BMG Gear Ratio)
##  Use 80:20 for M4, M3.1
# gear_ratio: 50:17               #BMG Gear Ratio
microsteps: 16
full_steps_per_rotation: 200    #200 for 1.8 degree, 400 for 0.9 degree
nozzle_diameter: 0.400
filament_diameter: 1.75
heater_pin: PE3
##  Validate the following thermistor type to make sure it is correct
##  See https://www.klipper3d.org/Config_Reference.html#common-thermistors for additional options
sensor_type: Trianglelab NTC100K B3950
# sensor_type: ATC Semitec 104GT-2
sensor_pin: PA1
min_temp: 10
max_temp: 270
max_power: 1.0
min_extrude_temp: 170
#control: pid
#pid_kp: 26.213
#pid_ki: 1.304
#pid_kd: 131.721
##  Try to keep pressure_advance below 1.0
pressure_advance: 0.045
##  Default is 0.040, leave stock
pressure_advance_smooth_time: 0.040

[thermistor Trianglelab NTC100K B3950]
## values calibrated against a PT100 reference
temperature1: 25.0
resistance1: 103180.0
temperature2: 150.0
resistance2: 1366.2
temperature3: 250.0
resistance3: 168.6

##  E0 on MOTOR6
##  Make sure to update below for your relevant driver (2208 or 2209)
#[tmc5160 extruder]
[tmc2209 extruder]
uart_pin: PF8
interpolate: False
run_current: 0.5
# hold_current: 0.6
sense_resistor: 0.110
stealthchop_threshold: 0 # 999999


#####################################################################
#   Bed Heater
#####################################################################

[heater_bed]
##  SSR Pin - HE1
##  Thermistor - TB
heater_pin: PB7
##  Validate the following thermistor type to make sure it is correct
##  See https://www.klipper3d.org/Config_Reference.html#common-thermistors for additional options
sensor_type: EPCOS 100K B57560G104F
# sensor_type: ATC Semitec 104GT-2
sensor_pin: PA0
##  Adjust Max Power so your heater doesn't warp your bed. Rule of thumb is 0.4 watts / cm^2 .
max_power: 1.0
min_temp: 0
max_temp: 120
#control: pid
#pid_kp: 58.437
#pid_ki: 2.347
#pid_kd: 363.769

[verify_heater heater_bed]
heating_gain: 1
check_gain_time:120
hysteresis: 10
max_error: 130

#####################################################################
#   Probe
#####################################################################

[probe]
#x_offset: 0
#y_offset: 25.0
#z_offset: 0
#speed: 15.0
#;z_hop: 3
#;z_hop_speed:40.0
#lift_speed: 40.0
#samples: 2
#samples_result: median
#sample_retract_dist: 2.0
#samples_tolerance: 0.006
#samples_tolerance_retries: 3

#####################################################################
#	Thermistor for ambient temperature
#####################################################################

#[temperature_sensor chamber]
# sensor_type: ATC Semitec 104GT-2  # reads about 10 C low
#sensor_type: NTC 100K MGB18-104F39050L32
# sensor_type: Trianglelab NTC100K B3950
# sensor_type: Generic 3950  # fluctuates a lot around 50 C
#sensor_pin: PF5 # T1

#####################################################################
#   Fan Control
#####################################################################
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

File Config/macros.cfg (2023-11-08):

#####################################################################
#	User Macros
#####################################################################

[gcode_macro PREHEAT_PLA]
gcode:
  M104 S210                       ; set extruder to 210C
  M140 S55                        ; set bed temp to 55C

[gcode_macro PREHEAT_ABS]
gcode:
  M104 S250                       ; set extruder to 250C
  M140 S100                       ; set bed temp to 100C

[gcode_macro HEAT_SPREAD]
gcode:
  STATUS_STANDBY                  ; turn on LEDs
  G28                             ; home all axes
  G0 Z5 F4000                     ; move Z to 5mm above buildplate
  G0 X60 Y60 F6000                ; move toolhead to center of build plate
  M140 S100                       ; set bed temp to 100C
  M106 S204                       ; turn on part cooling fans at 80%

[gcode_macro PARK]
gcode:
  STATUS_STANDBY
  G28 X120 Y120
  G0 X60 Y60 Z50 F2600

#####################################################################
#	Macros
#####################################################################


[gcode_macro _PRINT_START]
#   Use PRINT_START for the slicer starting script - please customize for your slicer of choice
#   ATR  _PRINT_START tool_temp=[first_layer_temperature] bed_temp=[first_layer_bed_temperature]
gcode:
    {% set MATERIAL = params.MATERIAL|default('ABS')|string %}
    {% if MATERIAL == "PLA" %}
        # SET_PRESSURE_ADVANCE ADVANCE=0.035 SMOOTH_TIME=0.040
        # SET_GCODE_OFFSET Z=-0.0
    {% elif MATERIAL == "PET" %}
        # SET_PRESSURE_ADVANCE ADVANCE=0.035 SMOOTH_TIME=0.040
        # SET_GCODE_OFFSET Z=0.0
    {% elif MATERIAL == "ABS" %}
        # SET_PRESSURE_ADVANCE ADVANCE=0.035 SMOOTH_TIME=0.040
        # SET_GCODE_OFFSET Z=0.0
    {% else %}
        # SET_PRESSURE_ADVANCE ADVANCE=0.035 SMOOTH_TIME=0.040
        # SET_GCODE_OFFSET Z=0.0
    {% endif %}
    {% set TARGET = params.TARGET | default(0) %}
    {% set PERIOD = (params.PERIOD | default(3) | int) %} ## minutes

    STATUS_STANDBY
    M117 Homing...                 ; display message
    G28
    M117 Z Tilt Adjust...
    Z_TILT_ADJUST

    G90 ; use absolute coordinates
    M83 ; extruder relative mode

    M117 Center toolhead
    G0 X90 Y90 Z5 F6000            ; center toolhead on build platform
    M106 S204                      ; turn on part cooling fans at 80%
    M117 Heating bed
    M140 S{ params.BED_TEMP }      ; set bed temp
    # HEAT_SPREAD
    M190 S{ params.BED_TEMP }      ; wait for bed temp
    M106 S0                        ; turn off part cooling fans
    G28 Z0                         ; home Z with bed up to temperature

    ;RESPOND TYPE=command MSG="will soak for { PERIOD }m"
    M117 Soaking for { PERIOD }m
    G4 P{ PERIOD * 1000 * 60 }

    M104 S150                      ; warm up nozzle
    M117 Mesh leveling...          ; display message
    ; G28                          ; home all without mesh bed level
    BED_MESH_CALIBRATE
    G0 X90 Y90 Z10 F18000          ; re-center toolhead

    M117 Heating Hotend...
    G1 X175 Y175 Z0.1 F4000        ; move to position to minimize oozing
    M104 S{ params.TOOL_TEMP }	   ; set extruder temp
    M109 S{ params.TOOL_TEMP }     ; wait for extruder temp

    M117 Priming ...
    G28
    G1 X2.0 Y8.0 F18000            ; go to edge of bed
    G1 Z0.2 F5000                  ; lower nozzle
    G92 E0.0
    G1 X40.0 E7.0 F1000.0          ; intro line
    G1 X80.0 E8.0 F1000.0          ; intro line
    G92 E0.0

    STATUS_READY
    M117                           ; clear display message
    G1 Z1 F5000                    ; lift nozzle
   
[gcode_macro _PRINT_END]
#   Use PRINT_END for the slicer ending script - please customize for your slicer of choice
gcode:
    M400                           ; wait for buffer to clear
    G92 E0                         ; zero the extruder
    G1 E-4.0 F3600                 ; retract filament
    TURN_OFF_HEATERS
    M107                           ; turn off fan
    G91                            ; relative positioning
    G0  Z20 F3600                  ; lift nozzle
    G90                            ; absolute positioning
    G0 X175 Y175                   ; move printhead out of the way
    ;G28 Y120                      ; home y axis
    M84                            ; disable motors
    STATUS_STANDBY


;    #   Get Boundaries
;    {% set max_x = printer.configfile.config["stepper_x"]["position_max"]|float %}
;    {% set max_y = printer.configfile.config["stepper_y"]["position_max"]|float %}
;    {% set max_z = printer.configfile.config["stepper_z"]["position_max"]|float %}

    #   Check end position to determine safe direction to move
;    {% if printer.toolhead.position.x < (max_x - 20) %}
;        {% set x_safe = 20.0 %}
;    {% else %}
;        {% set x_safe = -20.0 %}
;    {% endif %}

;    {% if printer.toolhead.position.y < (max_y - 20) %}
;        {% set y_safe = 20.0 %}
;    {% else %}
;        {% set y_safe = -20.0 %}
;    {% endif %}

;    {% if printer.toolhead.position.z < (max_z - 2) %}
;        {% set z_safe = 2.0 %}
;    {% else %}
;        {% set z_safe = max_z - printer.toolhead.position.z %}
;    {% endif %}

;    G0 Z{z_safe} F3600             ; move nozzle up
;    G0 X{x_safe} Y{y_safe} F20000  ; move nozzle to remove stringing
;    TURN_OFF_HEATERS
;    M107                           ; turn off fan
;    G90                            ; absolute positioning
;    G0 X60 Y{max_y} F3600          ; park nozzle at rear
	
[gcode_macro LOAD_FILAMENT]
gcode:
   M83                            ; set extruder to relative
   G1 E30 F300                    ; load
   G1 E15 F150                    ; prime nozzle with filament
   G1 E-3 F200                    ; retract a little to minimize oozing
   M82                            ; set extruder to absolute
    
[gcode_macro UNLOAD_FILAMENT]
gcode:
   M83                            ; set extruder to relative
   G1 E6 F300                     ; extrude a little to soften tip
   G1 E-40 F1800                  ; retract some, but not too much or it will jam
   M82                            ; set extruder to absolute

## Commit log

2023-11-08 Update folder
    [3mm_back_aux_panel_black.stl, 3mm_back_main_panel_black.stl, 3mm_door_panel_clear.stl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]
2023-11-09 File structure clean-up
    [3mm_back_aux_panel_black.stl, 3mm_back_main_panel_black.stl, 3mm_door_panel_clear.stl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]
2023-11-09 added tophat closing chamfer
    [[b]_Frame_front_upper_left.stl, [b]_Frame_front_upper_right.stl]
2023-11-09 Add image of geared Z options
2023-11-09 Added picture of flexure joint
2023-11-09 Fix stl errors and file clean-up
    [Calibration_square_100mm_base.stl, Printed_Parts.xls, [a]_door_panel_pinch_handle_x2.stl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]
2023-11-10 Fixed .stl errors
    [[a]_Motor_mount_rear_Nema14.stl, [a]_Motor_mount_rear_Nema17.stl, [a]_Z_axis_drive_rear_Nema14.stl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]
2023-11-10 Updated Assembly Manual - WIP
2023-11-11 Added .stl files
    [Printed_Parts.xls, [p]_12864_display_case_rear.stl, [p]_x_frame_Mini_Stealth_MicroProbe_left.stl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]
2023-11-12 Update Assembly Manual WIP
2023-11-17 Update Assembly Manual - Vorpal 180_WIP.pdf
2023-12-15 Added unibody frame pieces
    For those with large printers
    [[b]_Frame_Left_lower.stl, [b]_Frame_Left_upper.stl, [b]_Frame_Right_lower.stl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]
2023-12-15 Added Z carriages for UHF hotends
    [[p]_Z_carriage_left_UHF.stl, [p]_Z_carriage_rear_UHF.stl, [p]_Z_carriage_right_UHF.stl]
2024-08-04 Added Trident version of Bed Flexures
    [z_bed_left_M3_Flexure.stl, z_bed_rear_M3_Flexure.stl, z_bed_right_M3_Flexure.stl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]
